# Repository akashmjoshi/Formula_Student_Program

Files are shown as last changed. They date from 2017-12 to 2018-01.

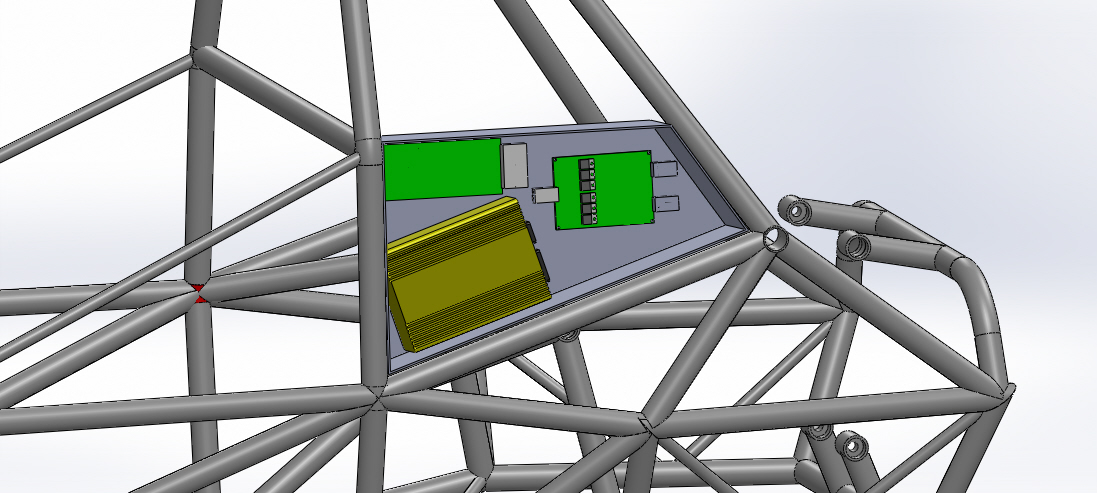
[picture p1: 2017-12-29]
documents/images/electronic assembly.JPG

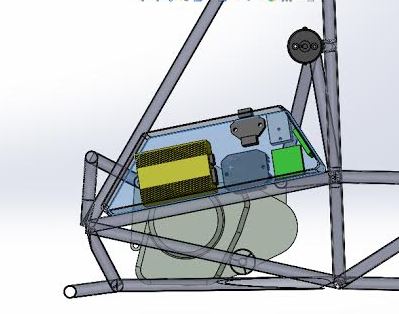
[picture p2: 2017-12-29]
documents/images/ELectronic_hub_casing_CAD.JPG

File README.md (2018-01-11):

# Formula_Student_Program
# Responsiblity
• Established CAN communication with Motec M400 (ECU) to display real-time sensor data on the steering-wheel
• Designed and manufactured a non-contact infrared tire-temperature and brake disc temperature data logger
• Performed Gear-Change Ignition Cut using a electronic-solenoid to perform clutch-less gear shifting
• Tuned the fuel and ignition maps during chassis-dyno to achieve a flat torque curve and optimize fuel efficiency  
•  Created a Wiki-System to allow proper flow of data among all subsystems of the team - https://sites.google.com/a/orion-racing.com/orion-wiki-test/

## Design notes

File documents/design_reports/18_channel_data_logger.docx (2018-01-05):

Data Acquisition System

Power Supply : A 12 V Li ion (or li po. Not sure) rechargeable battery is used. The battery can power t Data acquisition system for up to 7 hours continuously with full charge. The battery was incorporated to keep the DAQ an independent unit on the car.

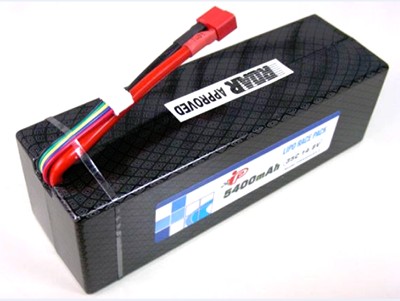
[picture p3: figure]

Power Card: The output of the power card is 3.3 V and 5 V. The voltages were chosen because

1) The dspic controller works on 3.3V
2) The ICs work on 5V supply

All the sensors are given 3.3V as supply voltage.

Parallel Port connectors are used to make the wiring and connections neater and less troublesome.

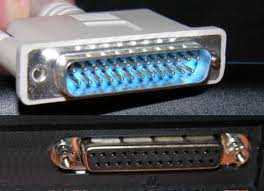
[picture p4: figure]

The Main Control board:

DAQ uses Dspic microcontroller. Some specification of the controller is shown below

Dspic33fj128gp706a

Device Pins: 64

Program : 128Kb

Flash:

Memory

(Kbyte)

RAM

(Kbyte)(1)

16-bit Timer

Input Capture

Output Compare

Std. PWM

Codec

Interface

ADC

UART

SPI

I2C™

Enhanced

CAN

I/O Pins (Max)(2)

Packages

The data collected from the sensors is analog in nature. The data is then converted into digital data using the ADC. The resolution of the system is 0.8mV.The data is then calibrated using equations which are acquired using Matlab. The data is then stored in Flash drive and is also seen on hyper terminal wirelessly.

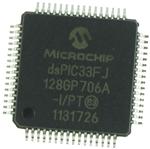
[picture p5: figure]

Modes of Logging Data:

1) USB Flash Drive using VINCULUM V Drive 2

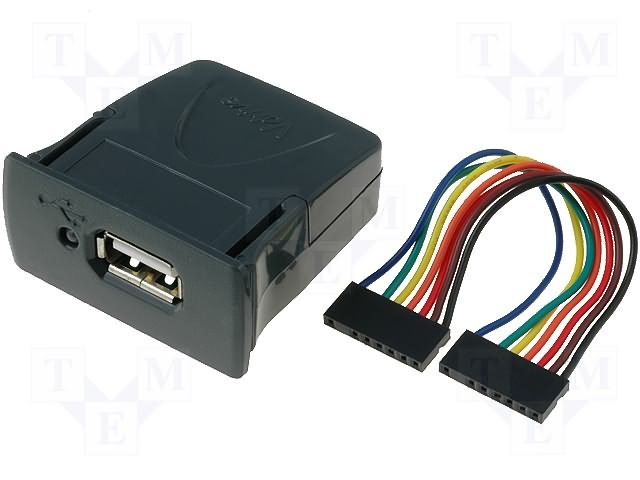
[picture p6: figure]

The Data from the Adc is stored in the Vdrive using Uart protocol. The baud rate for data transmission was set at 230400 for 4 channels. For the channels to be increased from 4 to 18 the baud rate was sacrificed and brought down to 38400.

The data acquired is stored in the USB flash drive in the form of an excel sheet in .xls format which can be easily viewed and analyzed.

2)Telemetry using X bee.

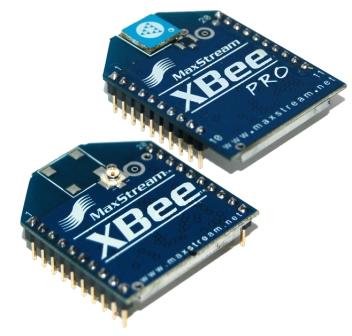
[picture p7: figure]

The data is seen live on the hyper terminal using xbee and the baud rate of the xbee was kept at 57600 even after changing the number of channels.

Indoor/Urban Range Up to 100 ft (30 m) Up to 300 ft. (90 m), up to 200 ft (60 m) International

variant

Outdoor RF line-of-sight Range Up to 300 ft (90 m) Up to 1 mile (1600 m), up to 2500 ft (750 m)

international variant

Transmit Power Output

(software selectable) 1mW (0 dBm) 63mW (18dBm)*

10mW (10 dBm) for International variant.

The data is also seen on the GUIs which are made on Labview. They are used for the ease of Analyzing.

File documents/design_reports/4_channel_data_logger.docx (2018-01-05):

DESIGN REPORT

ELECTRONICS

DATA ACQUISITION SYSTEM

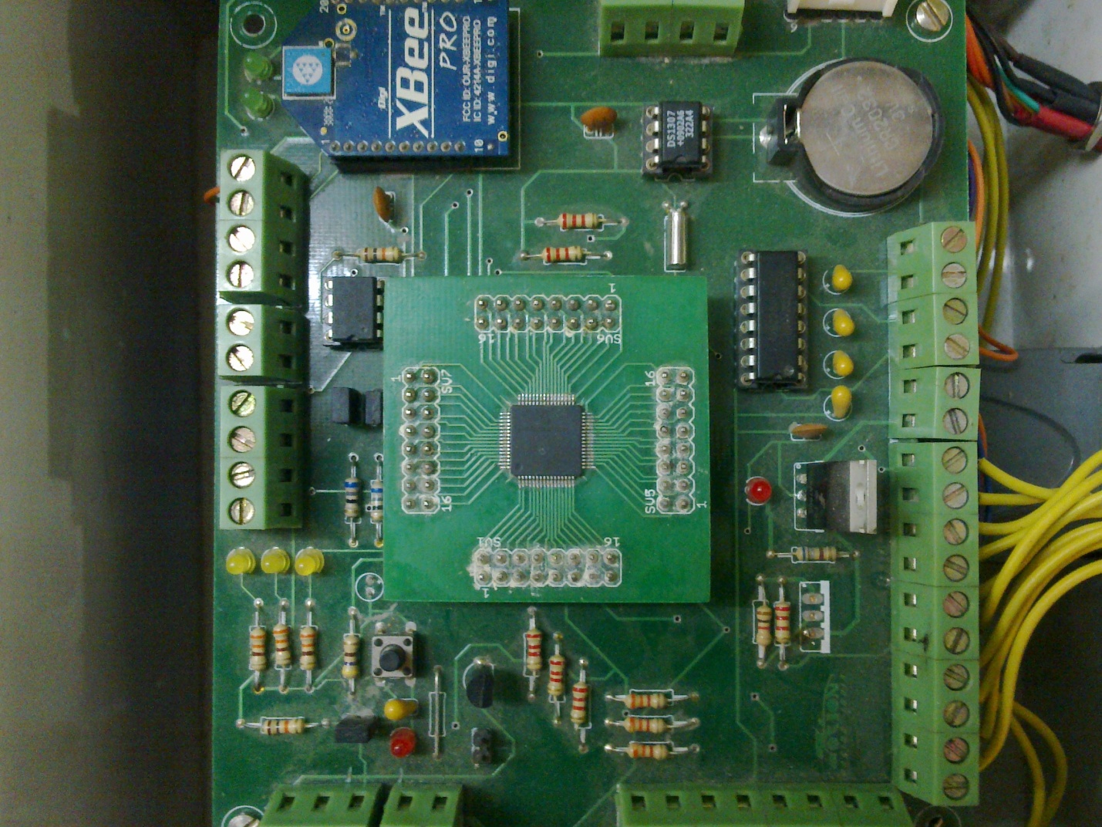
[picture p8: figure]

At present our data acquisition system uses a DSPIC33FJ128GP706A microcontroller. It has 18 analog channels which take in analog voltages and converts it into digital data and stores it into a USB flash drive

Last year the capacity of our data acquisition system was four channels. This year we modified the code and now the capacity has increased to eighteen channels, allowing us top log eighteen different sensors simultaneously.

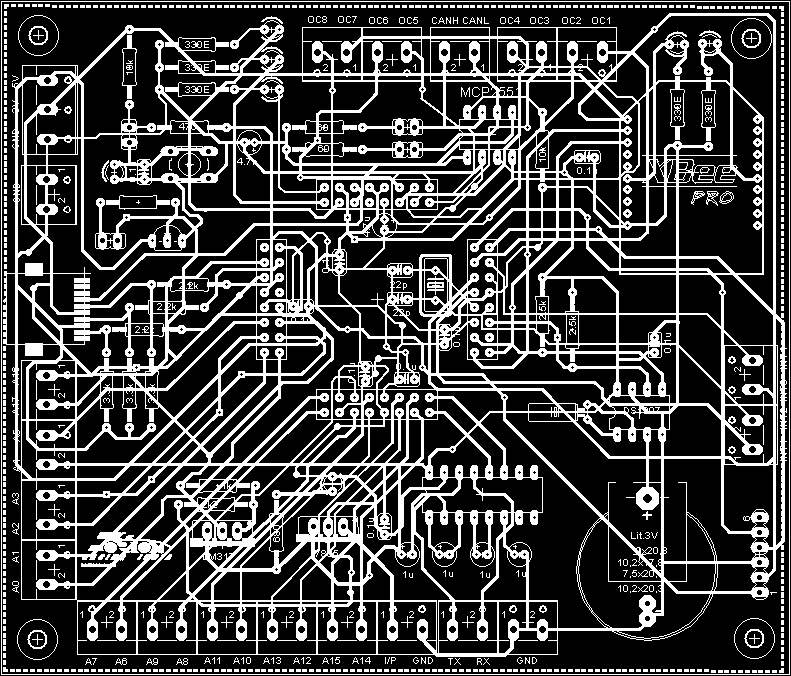
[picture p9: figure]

Since last year the DAQ had only four channels, the logging rate for the system was 125Hz, which was quite high. But now we have increased the number of channels to 18 thus the logging rate had to be reduced. In order to perfectly log the data we have kept the logging rate to 25Hz. Due to this change our baud rate had to be modified to 38400 from 57600. We are using a peripheral device called VDRIVE to log the data into the flash drive from the microcontroller. VDRIVE acts as the interface between the microcontroller and the flash drive. VDRIVE supports the USB 2.0 protocol.

The casing of our DAQ is too large and has unnecessary space. So this year we decided to change the casing of the DAQ. We have reduced the size of the casing and also changed the colour of the box to black so it would go better with the surroundings. The new case of the DAQ has helped us to save space and also to reduce weight.

Acquisition

1. STS

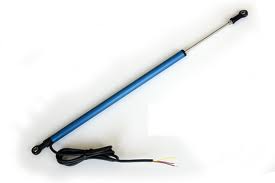
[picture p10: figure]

Shock travel sensor is a linear potentiometer which provides voltage as output

proportional to the position of the slider. When the wheel lifts up from the ground shaft of the sensor tends to move which in turn provides output in terms of voltage. This voltage is sent to the analog channel pin of the micro controller. Use: Suspension

2. ACCELEROMETER

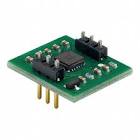
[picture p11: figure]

Accelerometers are used for measuring the g-force experienced by a body. The accelerometer that we use has the capability to measure all the 3-axis viz x,y,z.

The maximum g-force that can be measured by our accelerometer is 3g which is sufficient for our purpose. This voltage is sent to the analog channel pin of the micro controller.

Use: Chassis System

3. Steering Angle Sensor

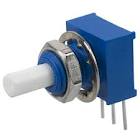
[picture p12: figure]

This is a rotational potentiometer. The output is an analog varying voltage which changes according to the angle of the steering wheel. This voltage is sent to the analog channel pin of the micro controller.

Use: Steering System

4. Gear Position Sensor

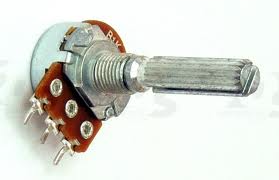
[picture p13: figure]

This is a rotational potentiometer. The output is an analog varying voltage which changes according to the angle of the steering wheel. This voltage is sent to the analog channel pin of the micro controller.

Use: Engine System

5. Fuel Level Indicator

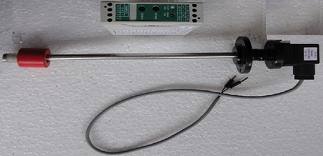
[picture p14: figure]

This is an angular potentiometer. There is a shaft that varies with the level of the fuel. Corresponding to that a analog voltage is produced. This voltage is sent to the analog channel pin of the micro controller.

Use: fuel tank

6. Wheel Speed Sensor

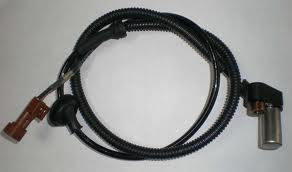
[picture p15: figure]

The wheel speed sensor provides us with the information to calculate the wheel speed of the automobile. Our wheel speed sensor works on the Hall effect principle. It provides us with PWM pulses. These pulses can be directly sent to the PWM pins of the microcontroller which can then be logged in the usb flash drive. We can also use a RC network to convert the PWM pulses to analog voltage and then log it in our system.

Use: Suspension

7. Break Pressure Sensor

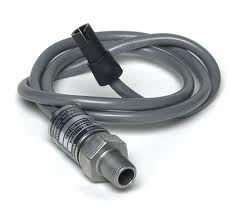
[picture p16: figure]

The brake pressure sensor provides the information about the pressure applied on the brake pedal. The output of this sensor is a varying current. We will be using an I to V converter in order to log data from this sensor. This voltage is sent to the analog channel pin of the micro controller.

Use: Brake System

Calibration of the sensors was done to ensure proper output. We used MATLAB and LABVIEW to calibrate the sensors. Our microcontroller has a 12-bit ADC. Thus we get a digital output of 0-4095 corresponding to analog voltage of 0-3.3 respectively. We took various reading of the sensor using live telemetry and with the help of LABVIEW. We noted down the readings of the sensor output and plotted the graph in MATLAB. MATLAB was able to provide us with the equation of the graph. Now in our daq code we inserted that equation and hence we were able to take proper reading of the sensor

WIRING

Previously for the relays and the fuses we had separate boxes. This arrangement made troubleshooting difficult for us. To overcome this problem what we have done is that we mounted all the relays on the firewall. This has made assembling the relays and the wiring easier. Also now we have a separate fuse case for every fuse as opposed to last year’s fuse box. This way routing the wires has become easier and also it has helped us to reduce the length of the wires.

Another improvement that we have made is the use of heat shrinks. Last year we had used wire sleeves. The problem with wire sleeves was that due to bending of the wires there was a chance that the wires would snap. The heat shrinks do not pose any problem as such. Another advantage of heat shrinks is that they look good aesthetically, they go with the car.

Majority of the wiring has been done using 4mm gauge wire. The starter motor, main kill and fuel pump have been wired using 8mm wire gauge.

The dashboard contains switches for the MOTEC(our ECU), kill, fan, cooling pump, rain-mode and the lcd.

We bought these professional type connectors. But then we realised later that these are not suitable for our task as the crimps were getting loose all the time and we were facing connectivity issues. The crimps would incessantly become loose and would come out of its connector. The new connectors that we bought solved that problem, they are better because the crimps do not get loose and connectivity is maintained during running of the car.

The wiring has also increased as the DAQ has eighteen channels and so all the 18 analog channel needs to be wired with its respective sensor.

DRIVER INTERFACE

LCD on the steering wheel: we are mounting a 20*4 LCD on the steering wheel to display information to the driver. The information to be displayed includes speed, distance, fuel level, gear position. The LCD is controlled by a PIC18F4520 microcontroller. This controller was chosen because of its ability to get data from 13 different channels using one inbuilt analog to digital convertor. The LCD is controlled in a 4 bit mode for port optimization. Data is taken from the engine as well as the sensors attached on the car. This data is then calibrated and displayed on the LCD. Odometer is also being displayed on the LCD screen and to achieve that we have used the FLASH Memory of the controller to store the odometer reading so that the data is not lost after power off. The LCD code is designed in such a way that a small switch is used to switch the screen from one to another on the same LCD.

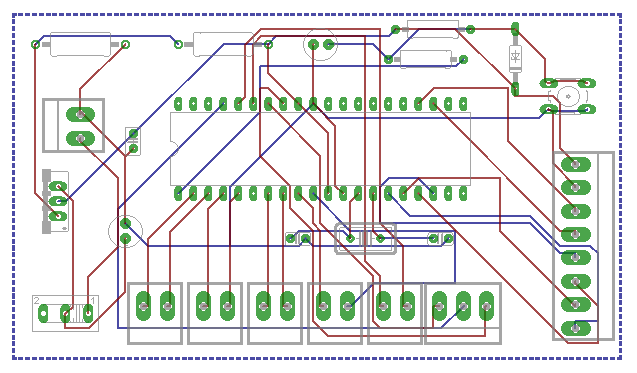
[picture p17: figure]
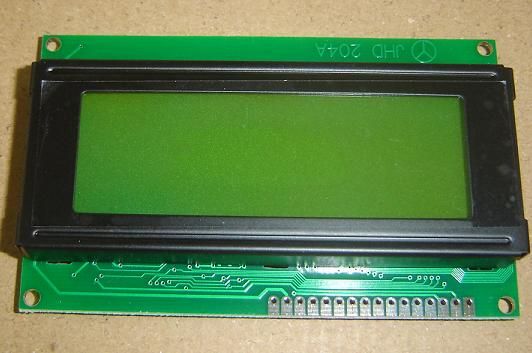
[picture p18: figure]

RPM SHIFT LIGHTS: This year instead of having two separate circuits for the LED’s we are using a single circuit. This way it saves power and space. The steering wheel does not have enough spacing for a pcb as large as last year’s so we have made a small circuit. We need last year’s circuit photograph for comparison

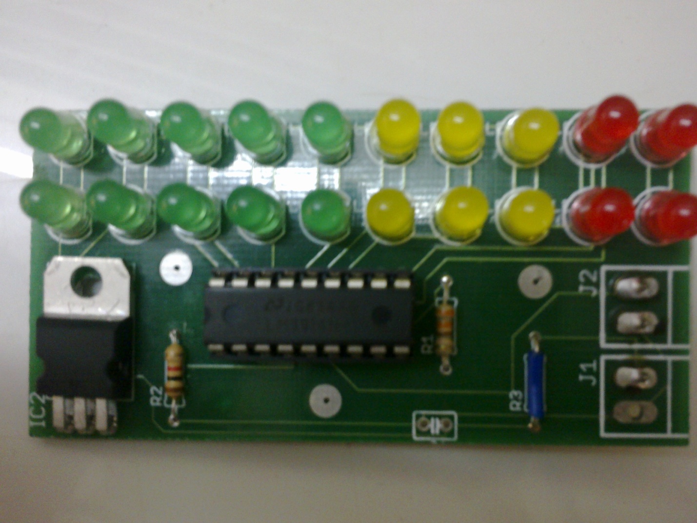
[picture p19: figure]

The circuit consists of LM 3914 which is a bar/dot display driver. A maximum of 10 led’s can be driven. The LED’s are driven according to the voltage variation at the signal pin of the IC which is pin no.5. The signal from the ECU for engine revolution was a varying frequency signal. We thought of using a capacitor with a bleeder resistor but it did not work out. We are now using IC LM 2907 which is a frequency to voltage convertor. This IC converts the frequency from the signal and converts it into analog voltage at 1V/67Hz. LM 7808 is used for regulated voltage supply to the IC.

RPM Shift Lights lets the driver know when to shift gear through the lighting of the led’s giving him a rough idea of the engine rpm.

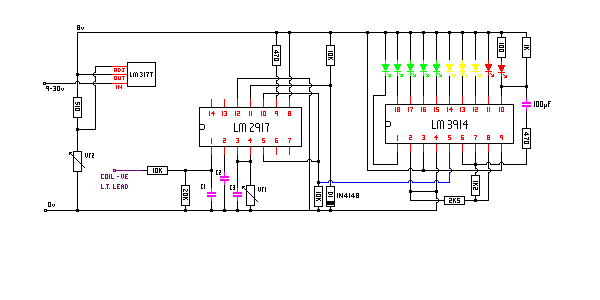
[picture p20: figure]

FUTURE IMPROVEMENTS:

We have decided to use a graphic LCD display for next year for better visual display for the driver while driving the car. Implementation of RPM shifts lights on the LCD controller itself. This can be achieved by reducing the number or channels and making a PORT on the controller available for RPM output.

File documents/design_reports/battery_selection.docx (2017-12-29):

CHAPTER 2: BATTERY

System Needs

ECU MoTec M400

- The power is distributed among the fuel pump, ignition coils and injectors, and ignition module.
- The fuel pump consumes 8 amps @ 12 Volts to maintain fuel pressure at 50 psi.
- The injectors’ ohm values lie between 11.9 to 12.1 ohms. Considering 12.1 ohms resistance and battery voltage of 13.7 volts at idle, the average current consumed will be 1.13 amps.
- The ignition coils consumes 6 amps of current at every spark cycles.
- Total 15.13 amps of current is required.

Cooling System

- The cooling system consists of 2 motors; one used for the radiator fan and the second used as a water pump.
- The water pump motor is run at 5.7amps.
- The radiator fan motor consumes 5.5 amps
- Total 11 .2 amps of current is required.

The current required for gear position system and SLM consumes maximum 3 amps of current.

The cranking current is typical 35 amps of current, but this much current is needed only at the time of cranking. Therefore of 35 amps of current is required for 2 to 3 seconds.

Total maximum of 29.33 amps of current is needed for all systems to work properly.

During the testing sessions once the alternator was failed. Testing logs are as shown in fig.1

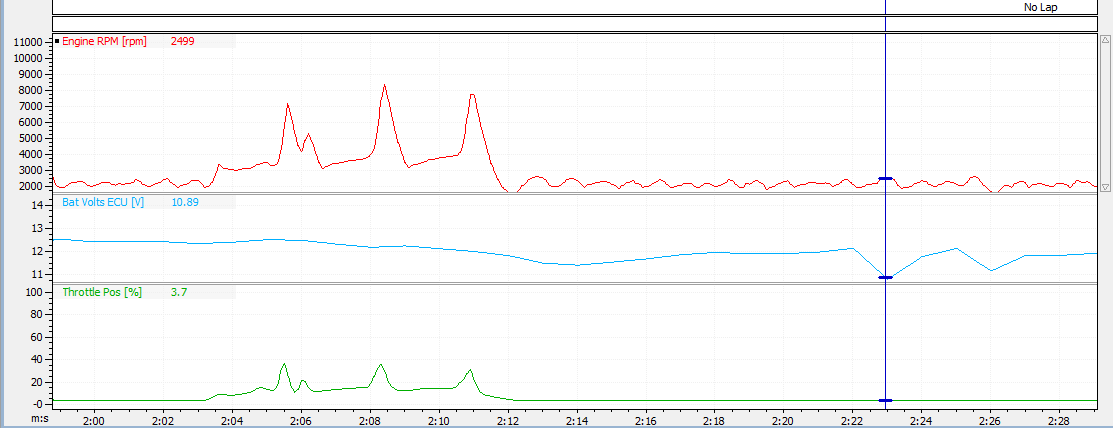
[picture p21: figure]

Fig.2.1

In case of accidental improper function of alternator, battery is supposed to provide 29.33 amps of current. Considering 96 seconds for one lap, 18 laps will takes 1728 seconds that is 28.8 minutes to complete the event. So battery is supposed to give at least 29.33 amps of current. Therefore we decided to use a 21 Ah battery which will be able to supply 42 ampere of current which will ensure the event gets completed with alternator failure.

The battery is placed between primary and secondary fire wall, and we have provision to remove the secondary fire wall as shown in the fig.2. Hence the battery can be easily accessed from outside after the removal of driver seat.

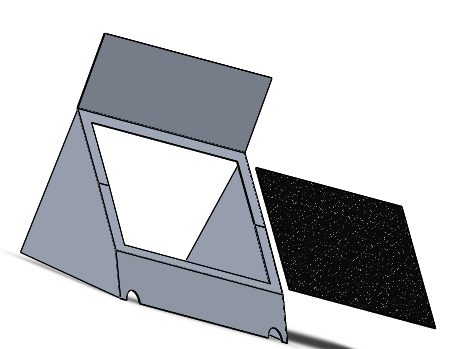
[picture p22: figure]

Fig.2.2

By giving the easy access to the battery, the debugging is also easy. So the debugging time gets reduced.

THE DECISION OF SELECTING LITHIUM ION BATTERY

The battery used in most cars is lead acid batteries but these prove to be too heavy for a formula student race car. Batteries need to be lighter and compact for better weight reduction and still provide the needed performance. The batteries need to be rechargeable through a rectifier connected to the alternator of the engine. Hence to justify our battery selection various decision and analysis were made.

Battery Selection Criteria

- Battery Weight : Lesser the better
- Battery Capacity (AH) : More the better
- Battery Discharge rate (Amp) : Less the Better
- Battery Cost : Less the better
- Battery Size (Volume) : Less the better

The Ah number indicates how many amps (how much current) a battery can supply over a given period of time. It's sort of the gas gauge of a battery's fuel tank. The higher the number, the more likely the battery will deliver prolonged performance.

We made a decision matrix as shown below to give weightages to the parameters which were more important than the other.

| weight | Discharge | cost | size
Weight | 1 | 1 | 1 | 0
discharge | 1 | 1 | 0 | 0
Cost | 1 | 0 | 1 | 0
Size | 0 | 0 | 0 | 1
Total | 3 | 2 | 2 | 1
weightage | 37.5 | 25 | 25 | 12.5
| | Table.2.1
Chemistry | weight | Discharge | cost | size
Lead Acid | 0 | 0 | 1 | 0
Lithium-iron | 1 | 1 | 0 | 1
Weighted | Weight | Discharge | Cost | Size | Total Score
Lead acid | 0 | 0 | 25 | 0 | 25
Lithium-iron | 37.5 | 25 | 0 | 12.5 | 75

Table.2.2

Here in table.1 we gave weightages to the parameters. The weightage points have been normalizes to a total of 100 points.

In table.2 we have compared Lead Acid Battery with the Lithium-ion battery. These batteries were found suitable by us for automotive use.

Adding up the scores from table one and two, we can see that the weightage total of the scores for Lithium-iron is higher than lead acid battery by 50 points. Advanced chemistry batteries include LiFePO4 batteries and Li Ion batteries. Batteries of these chemistries were found suitable by us for automotive use. Adding up the scores from table one and two, we can see that the weightage total of the scores for advanced chemistry is higher than lead acid battery by 50 points. Thus we justified the use of Advanced Chemistry batteries.

Shorai and braille were the two reliable batteries which we found suitable for automotive use. A comparison of shorai with the braille battery is as shown below. We have represented advanced chemistry batteries with the braille battery.

battery chemistries | Weight | discharge | | cost | size
LiFePO4 (Shorai) | 1 | 0 | | 1 | 1
Li Ion (Braille) | 0 | 1 | | 0 | 0
TOTAL | 1 | 1 | | 1 | 1
WEIGHTAGE | 25 | 25 | | 25 | 25
| | Table2.3
Weighted | Weight | Discharge | Cost | | Size | Weighted Score
LiFePO4 (Shorai) | 25 | 0 | 25 | | 25 | 75
Li Ion (Braille) | 0 | 25 | 0 | | 0 | 25

Table.2.4

Thus we have selected SHORAI LFX21A6-BS12. This battery weighs 1410 grams which is 740 grams higher than previous year’s battery. This was the compromise made in the battery selection procedure.

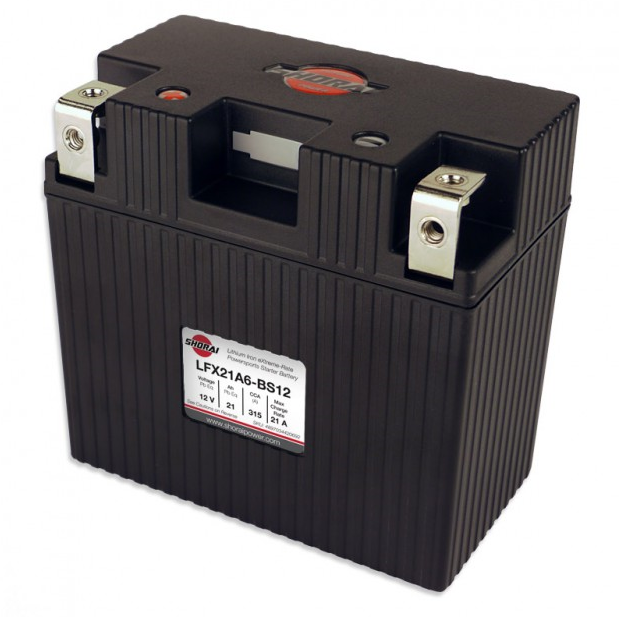
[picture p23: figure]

Advantages of using the selected battery:

- Ultra-light. One Fifth the weight of convectional batteries on average (1.41 kg/7.11kg)
- Zero sulfation, for longer service life
- More current for burst: (315 Amps)
- Military spec Carbon Composite Case
- Fast charging for better cranking
- No explosive gasses during charge
- No need of using a BMS

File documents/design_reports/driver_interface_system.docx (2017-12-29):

CHAPTER 4: DRIVER INTERFACE SYSTEM

Design Targets

1. Vehicular Interaction with the driver

Showing vital information to the driver such as rpm, engine temp, oil pressure, speed and fuel used.

2. Ergonomically placed steering system and dashboard

The way a driver interacts physically with the car is also important. This means the location of the steering wheel, the dashboard and shifter link play major role in driving feasibility. Thus an ergonomically designed driver interface system is a must.

3. Compactness and vehicular integration

The use of CAD models during PCB design to formulate a well-designed and compact system

System Design

The electronics system was designed along with the 3d model of the car which proved to be very reliable. The electronics systems are placed within the secondary and the primary firewall. This assured the temperatures never reached more than 60 degrees. The compactness of the secondary firewall provided a safety factor for the systems.

Secondly a high speed microcontroller was used to achieve refresh rates 67Hz as compared to 1Hz in our previous design. Sensor calibration was achieved using 5 point calibration technique to prevent linear hysteresis.

Electronics hardware integration within the steering wheel made the design and handling very user-friendly. The dashboard was made ergonomically and acquire minimum space and the cause least driver interference.

CAD / 3d part files and assembly was done on Solidworks to achieve accurate integration with other systems and it also provided an overlay for the wiring harness. The use of CAD was done for the first time and it proved really helpful in design and manufacturing.

Dashboard

The dashboard consist 3 switches; the cockpit kill switch, the cooling switch and the ignition switch. These are ground activated switches and are used to turn on relays. The cockpit kill switch is a push to break switch and disconnects the power supply to the ECU M400. This in turn turns off the supply to the fuel and ignition system thus stopping the engine.

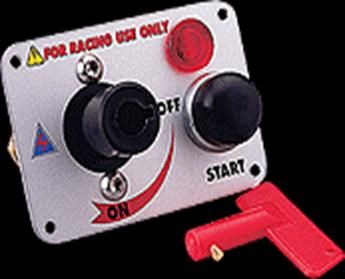
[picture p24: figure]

Fig 4.1

External Kill Switch

The cooling switch turns on and off a PCB mountable relay which in turn switch on or off the cooling centrifugal pump or the cooling fan.

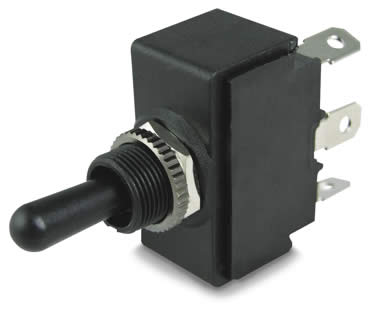
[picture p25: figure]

Fig 4.2

Cooling Switch

The ignition switch is ground connected to the automotive starter motor relay. The switch is a momentary switch and pressing the switch turns on the stator motor which help the engine to crank and synch the crankshaft and the flywheel.

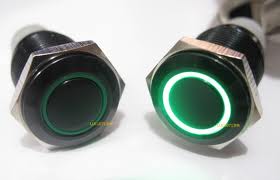
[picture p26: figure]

Fig 4.3

Ignition Switch

Steering Display System

The design phase started with what parameter was to be displayed on the screen.

The steering wheel is one of the most important parts of a formula race car. It needs to show vital engine parameters to the drivers during a long endurance run. The steering wheel is made of 7 series aluminum and the electronic system consists of a 7 segment display for showing gear. Two 4 digit 7 segment displays to show different engine parameters of the engine. There is a 16 bit RPM/GSL LEDs to tell the driver when to shift to get maximum torque in the next gear.

| | | | | | | | Output Shaft Torque
RPM | | Engine torque | | | | 1st | 2nd | 3rd | 4th | 5th | 6th
| | | | HP | Ratio :1 -> | 2.833 | 2.062 | 1.647 | 1.421 | 1.272
2000 | | 13.27 | | 5.1 | | 38 | 27 | 22 | 19 | 17 | 0
3000 | | 19.914 | | 11.4 | | 56 | 41 | 33 | 28 | 25 | 0
4000 | | 25.814 | | 19.7 | | 73 | 53 | 43 | 37 | 33 | 0
5000 | | 33.19 | | 31.6 | | 94 | 68 | 55 | 47 | 42 | 0
6000 | | 37.614 | | 43.0 | | 107 | 78 | 62 | 53 | 48 | 0
7000 | | 42.778 | | 57.0 | | 121 | 88 | 70 | 61 | 54 | 0
8000 | | 44.327 | | 67.5 | | 126 | 91 | 73 | 63 | 56 | 0
9000 | | 42.778 | | 73.3 | | 121 | 88 | 70 | 61 | 54 | 0
10000 | | 37.615 | | 71.6 | | 107 | 78 | 62 | 53 | 48 | 0
12000 | | 31.715 | | 72.5 | | 90 | 65 | 52 | 45 | 40 | 0

NOTE : The chart at left will help you find what RPM's each gear will jump to. It takes the gear ratios you entered, then calculates what RPM the next gear gives you. In the default scenario, if you shift at 5600 in each gear, then going to 2nd will drop you to 3300, from 2 to 3 (at 5600rpm) gets you at 3771, and so on.

To navigate, using the TAB key will produce the best results, and data entry areas are in blue.

This worksheet is protected, but no password is required . The BASELINE and DISCLAIMER are password protected.

Shift RPM

RPM after shift
| | | | | | | 1 - 2 | 2 - 3 | 3 - 4 | 4 - 5 | 5 - 6
| | | | | | 2000 | 1456 | 1597 | 1726 | 1790 | 0
| | | | | | 3000 | 2184 | 2396 | 2588 | 2685 | 0
| | | | | | 4000 | 2911 | 3195 | 3451 | 3581 | 0
| | | | | | 5000 | 3639 | 3994 | 4314 | 4476 | 0
| | | | | | 6000 | 4367 | 4792 | 5177 | 5371 | 0
| | | | | | 7000 | 5095 | 5591 | 6039 | 6266 | 0
| | | | | | 8000 | 5823 | 6390 | 6902 | 7161 | 0
| | | | | | 9000 | 6551 | 7189 | 7765 | 8056 | 0
| | | | | | 10000 | 7279 | 7987 | 8628 | 8951 | 0
| | | | | | 12000 | 8734 | 9585 | 10353 | 10742 | 0

Fig 4.4

RPM v/s Horse Power

The microcontroller used to control the display unit is a PIC18F6720 microcontroller. The microcontroller has timer circuits to detect RPM and analog channels to measure engine sensor values. This microcontroller was chosen based on its ability to provide a range of input output ports.

Microcontroller Specifications

High-Performance RISC CPU:

• C compiler optimized architecture/instruction set:

- Source code compatible with the PIC16 and PIC17 instruction sets

• Linear program memory addressing to 128 Kbytes

• Linear data memory addressing to 3840 bytes

• 1 Kbyte of data EEPROM

• Up to 10 MIPs operation:

- DC – 40 MHz osc./clock input

- 4 MHz – 10 MHz osc./clock input with PLL active

• 16-bit wide instructions, 8-bit wide data path

• Priority levels for interrupts

• 31-level, software accessible hardware stack

• 8 x 8 Single Cycle Hardware Multiplier External Memory Interface (PIC18F8X20 Devices Only):

• Address capability of up to 2 Mbytes

• 16-bit interface

Peripheral Features:

• High current sink/source 25 mA/25 mA

• Four external interrupt pins

• Timer0 module: 8-bit/16-bit timer/counter

• Timer1 module: 16-bit timer/counter

• Timer2 module: 8-bit timer/counter

• Timer3 module: 16-bit timer/counter

• Timer4 module: 8-bit timer/counter

• Secondary oscillator clock option – Timer1/Timer3

• Five Capture/Compare/PWM (CCP) modules:

- Capture is 16-bit, max. Resolution 6.25 ns (TCY/16)

- Compare is 16-bit, max. Resolution 100 ns (TCY

- PWM output: PWM resolution is 1 to 10-bit

• Master Synchronous Serial Port (MSSP) module with two modes of operation:

- 3-wire SPI™ (supports all 4 SPI modes) 2-I C™ Master and Slave mode

• Two Addressable USART modules:

- Supports RS-485 and RS-232

• Parallel Slave Port (PSP) module

Analog Features:

• 10-bit, up to 16-channel Analog-to-Digital Converter (A/D):

- Conversion available during Sleep

• Programmable 16-level Low-Voltage Detection (LVD) module:

- Supports interrupt on Low-Voltage Detection

• Programmable Brown-out Reset (PBOR)

• Dual analog comparators:

- Programmable input/output configuration

Special Microcontroller Features:

• 100,000 erase/write cycle Enhanced Flash program memory typical

• 1,000,000 erase/write cycle Data EEPROM memory typical

• 1 second programming time

• Flash/Data EEPROM Retention: > 40 years

• Self-reprogrammable under software control

• Power-on Reset (POR), Power-up Timer (PWRT) and Oscillator Start-up Timer (OST)

• Watchdog Timer (WDT) with its own On-Chip RC Oscillator for reliable operation

• Programmable code protection

• Power saving Sleep mode

• Selectable oscillator options including:

- 4X Phase Lock Loop (of primary oscillator)

- Secondary Oscillator (32 kHz) clock input

• In-Circuit Serial Programming™ (ICSP™) via two pins

• MPLAB ® In-Circuit Debug (ICD) via two pins


Fig 4.6

Driver Interface system


Fig 4.7

Steering Wheel

Coding and Testing

The code was written using Mikroc along with simulation in Proteus

Code:

//Decleration and Initialization

#include <built_in.h>

char ur,tr,hr,thr,ul,tl,hl,thl; //segment choping variables

int count,i,j,value,rpm,gearp;

char teeth;

int volt,etmp,as,ts;

int seg7(int num)

{

int val[]={0x3f,0x06,0x5b,0x4f,0x66,0x6D,0x7D,0x07,0x7F,0x6F,0x77,0x7C,0x39,0x5E,0x79,0x71};

return(val[num]);

}

int gear(int num)

{

int val[]={0x54,0x06,0xDA,0xCE,0x66,0xEC,0xFC,0x86,0xFE,0xEE};

return(val[num]);

}

int fun(int num)

{

int val[]={0x7f,0x3f,0x1f,0x1e,0x1c,0x18,0x10,0x18,0x1c,0x1e,0x1f,0x3f,0x7f,0x00,0x7f};

return(val[num]);

}

int bar(int num)

{

int val[]={0x81,0xc3,0xe7,0xff,0xe7,0xc3,0x81,0x81,0xc3,0xe7,0xff,0xe7,0xc3,0x81};

return(val[num]);

}

int gps()

{

j=ADC_READ(3);

if (j>=0 &&j<88)

{PORTB=gear(1);

return 1;}

// else if (j>=151 && j<159)

// {PORTB=gear(0);

// return 0;}

else if (j>=89 && j<284)

{PORTB=gear(2);

return 2;}

else if (j>=285 && j<499)

{PORTB=gear(3);

return 3;}

else if (j>=500 && j<700)

{PORTB=gear(4);

return 4;}

else if (j>=700 && j<897)

{PORTB=gear(5);

return 5;}

else if (j>=898 && j<1020)

{PORTB=gear(6);

return 6;}

}

int et()

{

j= ADC_Read(0); //engine temp begins

return etmp= (6.4*j*j/100000 +-0.19*j + 126);

}

speed()

{

value=TMR1H;

//use timer 1 for speed anf fuel used calculations

}

fuelused()

{

//use timer 1 for speed anf fuel used calculations

}

rpmlights(int num)

{

switch(num)

{

case 1: PORTF=0x01; break;

case 2: PORTF=0x01; break;

case 3: PORTF=0x01; break;

case 4: PORTF=0x03; break;

case 5: PORTF=0x07; break;

case 6: PORTF=0x1f; break;

case 7: PORTF=0x3f; break;

case 8: PORTF=0x7F; break;

case 9: PORTF=0xff; break;

case 10: PORTF=0x1c; break;

case 11: PORTF=0x1C; break;

case 12: PORTF=0x1C; break;

}

}

segr()

{

thr=value/1000;

hr=value/100%10;

tr=value/10%10;

ur=value%10;

if(value>999)

{

RC7_bit=1;

RC6_bit=0;

RC5_bit=1;

RC4_bit=1;

PORTD=seg7(thr);

delay_us(1000);

}

if(value>99)

{

RC7_bit=0;

RC6_bit=1;

RC5_bit=1;

RC4_bit=1;

PORTD=seg7(hr);

delay_us(1000);

}

if(value>9)

{

RC7_bit=1;

RC6_bit=1;

RC5_bit=1;

RC4_bit=0;

PORTD=seg7(tr);

delay_us(1000);

}

if(value>=0)

{

RC7_bit=1;

RC6_bit=1;

RC5_bit=0;

RC4_bit=1;

PORTD=seg7(ur);

//delay_us(2500);

}

}

segl()

{

thl=value/1000;

hl=(value/100)%10;

tl=value/10%10;

ul=value%10;

if(value>999)

{

RG3_bit=1;

RG2_bit=0;

RG1_bit=1;

RG0_bit=1;

PORTE=seg7(thl);

delay_us(1000);

}

if(value>99)

{

RG3_bit=1;

RG2_bit=1;

RG1_bit=1;

RG0_bit=0;

PORTE=seg7(hl);

delay_us(1000);

}

if(value>9)

{

RG3_bit=1;

RG2_bit=1;

RG1_bit=0;

RG0_bit=1;

PORTE=seg7(tl);

delay_us(1000);

}

if(value>=0)

{

RG3_bit=0;

RG2_bit=1;

RG1_bit=1;

RG0_bit=1;

PORTE=seg7(ul);

//delay_us(2500);

}

}

void coolon()

{

RG3_bit=1;

RG2_bit=0;

RG1_bit=1;

RG0_bit=1;

PORTE=0x39;

delay_us(4000);

RG3_bit=1;

RG2_bit=1;

RG1_bit=0;

RG0_bit=1;

PORTE=0x3F;

delay_us(4000);

RG3_bit=0;

RG2_bit=1;

RG1_bit=1;

RG0_bit=1;

PORTE=0x54;

delay_us(4000);

}

void cooloff()

{

RG3_bit=1;

RG2_bit=0;

RG1_bit=1;

RG0_bit=1;

PORTE=0x39;

delay_us(4000);

RG3_bit=1;

RG2_bit=1;

RG1_bit=0;

RG0_bit=1;

PORTE=0x3F;

delay_us(4000);

RG3_bit=0;

RG2_bit=1;

RG1_bit=1;

RG0_bit=1;

PORTE=0x71;

delay_us(4000);

}

void engoff()

{

RC7_bit=1;

RC6_bit=0;

RC5_bit=1;

RC4_bit=1;

PORTD=0x79;

delay_us(4000);

RC7_bit=1;

RC6_bit=1;

RC5_bit=1;

RC4_bit=0;

PORTD=0x3F;

delay_us(4000);

RC7_bit=1;

RC6_bit=1;

RC5_bit=0;

RC4_bit=1;

PORTD=0x71;

delay_us(4000);

}

void main() {

T0CON=0XF8; // timer0 on, 8 bit mode, counter, falling edge, with no prescalar

T1CON=0x0B;

TRISA=0xFF;

ADCON1=0x00;

TRISF = 0;

TRISE = 0;

TRISB = 0;

TRISD = 0;

TRISC0_BIT=1;

TRISC1_BIT=1;

TRISC2_BIT=1;

TRISC3_BIT=1; // 1's inputs

TRISC4_BIT=0;

TRISC5_BIT=0;

TRISC6_BIT=0;

TRISC7_BIT=0; // 0's outputs

TRISG = 0x00;

for(i=0; i<=14; i++)

{

PORTF=bar(i);

PORTB=fun(i);

PORTD=PORTE=fun(i);

PORTG=0X00;

RC4_bit=RC5_bit=RC6_bit=RC7_bit=0;

delay_ms(60);

}

PORTF = 0x00;

while(1)

{

DELAY_MS(16);

gearp=gps();

teeth= TMR0L;

value=teeth*60;

rpm=value/1000;

while(value <1000)

{engoff();

teeth= TMR0L;

value=teeth*60;

if(ADC_Read(1)<= 350)

cooloff();

else

coolon();

}

rpmlights(rpm);

value = et();

segr();

fuelused();

speed();

segl();

// write code for right rotary switch//

TMR0L=0x00;

TMR1H=0x00;

}

}


Fig 4.8

Driver Interface System Simulation

Gear Change Ignition Cut

The MoTeC GCIC function is used to allow the driver to change gears without lifting the throttle or (in most cases) the clutch, it is also often referred to as “Flat Shift” or “Shift without Lift”. The system allows a short ignition or fuel cut and/or ignition timing retard to reduce the engine’s load on the transmission so that the gear can be changed. It is also possible to have the position of an Electronic Throttle (Drive by Wire) reduced for a short amount of time as well.

The function is designed with both H pattern and sequential, dog engagement gear boxes in mind, it should be noted that this function is not completely suitable for synchromesh gearboxes.

Cut Modes

Mode 1, Delay from next gear stable

This mode is only suitable when the ECU has a gear position input. The ignition cut starts as soon as a valid shift signal is detected and will hold for however long it takes for the gear position pot or gear calculation to detect the next gear has been reached or the Minimum RPM or Minimum Throttle Position have been reached. The Delay time starts when the new gear is detected to allow time for full engagement then the ignition is phased back in linearly over the recovery time.


Fig 4.9

Mode 2, Delay from Cut Signal

The Delay from Cut Signal mode starts the ignition cut when the cut source becomes active and runs for the user defined Delay time (as set in Delay Table). After the delay has timed out the ignition Recovery time starts.


Fig 4.10

Mode 3, Cut While Signal is active

This mode will simply cut the ignition for as long as the shift signal is active. No delay times are entered for this mode. Mode 3 is mainly designed for external gear box control systems that are able to send a GCIC signal to the ECU; the cut time is calculated in the external controller.


Fig 4.11

It can be seen from the previous two diagrams that the gear position does not affect the cut at all.

Cut Source

To make the GCIC system work the ECU needs a request that the driver wishes to make an up shift, there are a number of options for this. It is possible that race class rules may only allow certain methods for GCIC so the rule book will need to be checked.

1. A simple momentary (on/off) switch the driver activates when an up shift needs to be made

2. A momentary switch on the clutch pedal

3. The request can be started when the RPM Limiter is reached

4. A strain gauge may be installed on the gear lever

5. The request can be started based on a rate of reduction of throttle position

6. The up shift request can come from the request linked to the Gear Shift function

(“semi-auto” or controlled gearboxes)

How the gear request device or condition is setup can have a very large effect on the performance of the GCIC function. One fairly important aspect of a gearbox that cannot be ignored is the mechanical free play from moving the gear shift lever to moving the dog ring. Another factor is how much force should be used to “preload” the gearbox shift mechanism to get the best shifts. To make a positive shift the driver needs to move to gear lever enough so that all the free play is eliminated and then apply enough force so that when the GCIC starts the gearbox will move almost instantly. Some problems that can arise from incorrect setup of the shift request are:

1. If the request system does not allow the driver to move the gear lever far enough to remove all the free play in the gearbox the GCIC will start too early. Starting the GCIC too early will mean that the total cut time will have to be longer to compensate.

2. If the driver does not have enough “preload” force on the gear lever before the

GCIC starts the gearbox mechanism will not accelerate quickly, again needing a longer cut time to compensate.

3. If too much force is required to start the GCIC the driver may become fatigued or the gear box may be damaged.

1. Digital (Switched) Input

A switched input can be located almost anywhere within reach of the driver but the best logical solution is to have it located on the gear lever. The switch may also be located on the clutch pedal but this may defeat the purpose of GCIC where clutch less shifts are desired. Some racing classes specify a switch location, e.g. steering wheel but this, like a clutch switch, means that the drive must co-ordinate the state of GCIC and the moving of the gear lever correctly and repeatable to get the best performance.

The diagram below shows a basic example of a “double jointed” gear knob for a sequential gearbox where GCIC is only needed on the up shift. The knob is able to pivot for a short distance on the gear lever when pulled towards the rear; this activates the switch giving the ECU its GCIC request. It is recommended that the spring be adjustable for preload so that the correct amount of force can be applied before the GCIC function is started.


Fig 4.12

GCIC Switch

If an H pattern system is needed or GCIC is required for both up and down shifts on a sequential gearbox a dual switch setup can be made.

The switch can be wired to either a Digital input or a Switched (Analogue Temperature) input. A switch wired to a Digital input must connect the input to 0v to pull it low and can be normally open or normally closed, whether the request is active when the switch is open or closed can be selected with the Logic Polarity parameter.

A switch that is wired to a Switched (Analogue Temperature) input can be connected to a voltage higher than 5v as the trigger levels can be defined by the user but it is most common practice to connect the input to 0v via the switch the same as the Digital input. Again a normally open or normally closed switch can be used.

2. RPM Limit

The RPM limiter can be used to request GCIC. The GCIC function request is active when the driver reaches the RPM limit. This method does not require any extra sensors to be added to the car but the driver must be aware that any time they reach the limiter they will get prolonged engine cutting if a gear change is not desired at that time. Delay from next gear stable may not be suitable for this method.

3. Gearshift Force - Strain Gauge

The Strain Gauge works by being bonded onto the surface of an item, its electrical properties change as it is deformed by the small amounts of tension and compression in the item. For GCIC the strain gauge is bonded onto the front or back of the gear lever. As the driver puts force on the gear lever it bends slightly causing a change in signal form the strain gauge.

The voltage signal for a strain gauge is very small and must be amplified to become useful to the ECUs input. When considering bonding a strain gauge onto a gear lever a suitable strain gauge amplifier is needed, this can add a considerable amount to the cost of the system.

The major benefit of the strain gauge is that it is an analogue input with a voltage reading proportional to the drivers force on the gear lever. With the analogue input to the ECU the tuner is able to program the level of force needed to trigger the GCIC request. Another benefit is to be able to data log how the driver is using the gear lever with much more information made available when compared to a simple on/off switch.

The Strain Gauge amplifier’s output can be connected to either an Analogue Voltage input or an Analogue Temperature input although it must be noted that the signal will be slightly non-linear when connected to the Analogue Temperature input due to its internal 1K ohm, 5v pull-up.

When calibrating the Gear Shift Force channel there is no need for the reading to be completely correct as the force level for the request will be set later. As a basic setting the calibration for 5v = 100N will be acceptable, if a more accurate reading is desired a custom calibration (using a fish scale for example) may be required.

4. Throttle Position Reduction

The rate at which the throttle is reduced can be a request for the GCIC function. The request is active when a user defined rate of reduction (TP% per second) of the Throttle Position Channel is reached or exceeded.

This method does not require any additional sensors to be added to the vehicle. Again,

driver education and correct setup is needed as the function will not be able to determine if the driver has lifted the throttle for a gear change or if it is a correction for a loss of traction for example. Again, the delay from next gear stable mode may not be suitable for this method.

Thinking outside the square for experienced users some conditions could be used where no cut is applied (from the cut level table) if there is any wheel slip, allowing the driver to quickly lift the throttle without inadvertently requesting GCIC.

5. Gear Shift Function

The gear box control function will already have a request for an up-shift, so it is possible to link the two functions in software so that the GCIC is automatically triggered when an up-shift request is made by the driver.

6. Minimum RPM

A lower level of RPM is set so that the function cannot be requested. For example, if the car is being driven through the pit lane it would be unnecessary to have GCIC active for the slow shifting needed, the driver would most likely want to use the clutch.

The Minimum RPM can work in different ways in different modes so care must be taken in setup. For the Delay From Cut Signal and Cut While Signal Active modes the Minimum RPM is only a condition that needs to be met at the start of the request and will not affect the cut event once it has been started. For example: If the Minimum RPM is 5000rpm and the engine is at 5050rpm, the GCIC can start. Clearly the RPM will drop as soon as there is any cut. If the engine drops below 5000rpm while the GCIC event is going cut WILL NOT be stopped, the GCIC event will continue for its programmed time.

For the Delay from Next Gear Stable mode the minimum RPM is used in two ways, as a condition to allow the GCIC request to be valid and also as a safety measure for the RPM dropping to low. Because the Delay from Next Gear Stable mode can cut for a much longer time than the other two modes it is possible that the engine may stall if the driver makes a mistake.

7. Minimum Throttle Position

As per Minimum RPM there is also a parameter for a Minimum Throttle Position below which a request is ignored by the ECU. The different mode selected will affect how the Minimum Throttle is use in the same way as the Minimum RPM, for the Delay from Cut Signal and Cut While Signal Active modes the Minimum Throttle is used as a condition to allow the request and start the GCIC event, if the throttle position drops below this value during the GCIC event the cut will not be stopped, for the Delay From Next Gear Stable mode the Minimum Throttle is used as a condition to accept the request and if the throttle drops below this during the GCIC event the cut WILL be stopped.

Delay Table

The Delay Table sets the amount of time the ECU must cut the engine power so that the driver can make a successful shift. The Delay table works in two different ways depending on which Cut Mode is used.

For Mode 1, Delay from Next Gear Stable the request starts the cut and the ECU will continue to cut until the next gear is acquired or the Time Out period has elapsed. The Delay Table sets extra cut duration once the next gear has been reached; this allows time to ensure that the next gear has been successfully engaged. This time is generally short when compared to the Mode 2, Delay from Cut Signal and is often left as 0msecs.

For Mode 2, Delay from Cut Signal the Delay Table sets the time that the ECU cuts the engine power for, this time is started as soon as the cut request becomes active. Enough time must be allowed so that the driver is able to get to the next gear; this mode will not allow for mistakes and will reinstate the engine power after the Delay plus Recovery Time regardless of what position the gear box is in, see example below:


Fig 4.13

Driver Education

For drivers who have spent most of their racing career quickly lifting the throttle to change gear it can be quite difficult to convince them not to lift once GCIC function has been switched on. This can cause problems for the tuner who needs to set minimum and maximum values, especially throttle position, to make the function work. There are many cases of the driver not obeying the instruction to keep the throttle wide open on a shift and this can cause many problems for the logic of the function, below is a common example.

1. The driver has lowered the throttle position until it is well below the Minimum Throttle position.

2. The driver then pulls on the gear lever and is able to change gear with ease because there is no engine torque.

3. Because the driver is still holding enough force on the gear lever as the throttle is reapplied the cut starts. In this example the Mode was Delay from Next Gear Stable meaning that the cut is applied for the full Time Out because the driver triggered the GCIC request after the shift was made and not before.


Fig 4.14

Gear Shift Timing


Fig 4.15

Gear Shift Logged Data

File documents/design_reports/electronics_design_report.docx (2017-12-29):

ELECTRONICS DESIGN REPORT: ORION RACING INDIA

Team goal

While designing the car for reliability, the team looks forward to testing the car extensively for performance. System designs will be validated using sensor data and components will be tested in fatigue. Additionally, the sensors will provide us with data which will help us to tune the car. With the aid of a dynamometer, the aim is to improve and further tune the map table. By physically recreating event specific tracks, the performance of the vehicle is being improved upon.By integrating the above, the team hopes to realize its goal which is to complete and to compete.The design of the car was started by selection of the following three parameters.

1) Tire

Tire has been selected based on the TTC tire data which had 3 tires to compare namely Goodyear D2607, Hoosier and Continental 34M. On comparing the cornering characteristics for the vertical load that was assumed, the Goodyear gave a peak lateral force of 3870 N at 10° slip angle as compared to the Continental which gave a force of 3680 N at 6° slip angle. Keeping in mind the transient response, the Continental tire was selected. On comparing the acceleration characteristics the Continental gave a peak force of 2600N at 5° slip ratio. The low cost and availability of the tires further helped in finalizing the Continental. The increased weight of the Continental tire was a compromise between performance and weight.

2) Engine

With the team goal in mind, the car weight was assumed to be 230 to 240 kg. Thus power to weight ratio was made a main consideration and a 4 cylinder engine with higher displacement became the natural choice. Main criteria while choosing amongst the 4 cylinder engines were availability, torque, familiarity and previous experience. The F4i has 46 Nm of torque (stock) @ 10000 rpm which is more as compared to rest of the engines. The GSX has 46.5 Nm of torque (stock) but at a slightly higher engine rpm i.e. 10750. The peak power of F4i is 109 hp (stock) @ 12500 rpm which is more compared to the other engines. The YR6 has power output of 118 hp (stock) @ 13000 engine rpm but the cost of the engine is more and the torque is less (44.7 Nm @ 11750 engine rpm) as compared to the F4i.

3) Ergonomics

An ergonomic set-up was designed for two purposes:

1) To reduce driver fatigue by selecting an ergonomic position

2) To find the forces which the driver can apply

Each drivers' inputs have been considered and a position comfortable to each driver has been selected. These values acted as an input for designing the cockpit, pedal box, shifter system, seat and steering system. We also consulted a musculoskeletal specialist who helped us select the position in which the driver can apply maximum force with ease.

System Goal

Electronics

The goal for the electronics team this year is to design, build and implement an efficient electronics system which not only ensures higher reliability but also aides in vehicle analysis and tuning. The MoTec M400 ECU is selected over the Stock ECU based on its availability of features like launch and traction control, gear change ignition cut, the use of closed loop lambda control for dynamic fuel saving and one of the best GUI available for easy tuning.

The centralised telemetry system is self-designed to provide a wireless communication at 60MB/s over a range of 1 km and unlimited logging using a video capture system. The MoTec M400 data logging system is used to log sensor data at 200 Hz and i2 Standard is used to analyse the data. A sensor hub is made to provide plug and play of 14 sensor logging.

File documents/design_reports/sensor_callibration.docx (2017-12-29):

Chapter 5

Sensors and Calibration

List Of Sensors on the car:

- Accelerometer

- Air temperature sensor

- Brake pressure

- Engine temperature

- Exhaust gas temperature

- Fuel pressure sensor

- Lambda sensor

- Magnetic Sensor

- Oil pressure sensor

- Shock Travel Sensor

- Throttle position sensor

- Tire temperature

- Wheel Speed sensor

1. Accelerometer (Capacitive 3 - axis):

By virtue of its dimensions, characteristics and compatibility with gyroscopes, this 3 axis accelerometer allows the dynamic behaviour of the vehicle to be interpreted and checked.

The temperature compensation between - 20°C and 100°C allows the accelerometer to be used in extreme conditions.

This capacitive type 3 axis accelerometer, with a frequency range of up to 100 Hz, allows measurement of the acceleration of the constituent parts of the vehicle. The measuring range is from -5g to +5g.

Fig 5.1.a

3-axis Accelerometer

Calibration:


Fig 5.1.b

Longitudinal G Force Calibration


Fig 5.1.c

Vertical G Force Calibration


Fig 5.1.d

Lateral G Force Calibration

Logged Data:


Fig 5.1.e

Lateral & longitudinal G logged data

2. Air Temperature Sensor:

Air temperature sensor is a part of the AIE (air intake & exhaust) system on a car and is used to convert the engine intake air temperature into a voltage, which it then inputs into the engine control unit (ECU).

The engine control unit then uses this data to correct the rate of fuel injection to ensure the optimal use of fuel.

Fig 5.2.a

Inlet Air Temperature Sensor

Calibration:


Fig 5.2.b

Air Temperature Sensor calibration table

Logged Data:


Fig 5.2.c

Air Temperature Sensor logged data

3. Fluid Pressure Sensor (Brake/Fuel/Oil):

The pressure sensor gives voltage change with a change in fluid pressure. This sensor is used a brake pressure sensor, fuel pressure sensor and oil pressure sensor. The sensor used for different purposes is calibrated in the ECU.

Fig 5.3.a

Pressure Sensor

Calibration:


Fig 5.3.b

Brake Pressure Calibration


Fig 5.3.c

Fuel Pressure Calibration


Fig 5.3.d

Oil Pressure Calibration

Logged Data:


Fig 5.3.e

Brake Pressure Sensor logged data


Fig 5.3.f

Fuel Pressure Sensor logged data


Fig 5.3.g

Oil Pressure logged data

4. Engine Temperature Sensor:

An Engine Temperature Sensor (ETS) is a sensor that is screwed into the engine's block or cylinder head and is used to determine the temperature of the engine coolant. The sensor is basically a thermistor that changes resistance with temperature.

When the ETS is high (hotter), the resistance is low, and when the ETS is low (cooler) the resistance is high. This resistance reading is sent to the vehicle's ECU and can be used to activate emission controls or turn the engine's cooling fan on. The ETS sensor is usually a two wire sensor that uses a 5 volt reference from the ECU with a ground signal back to the ECU.

Fig 5.4.a

Engine Temperature Sensor

Calibration:


Fig 5.4.b

Engine Temperature Sensor Calibration

Logged Data:

Fig 5.4.c

Engine Temperature logged data

5. Exhaust Gas Temperature:

EGTs are resistance sensors whose resistance changes with change in temperature.

The resistance change cause voltage change and this voltage is calibrated in terms of temperature.


Fig 5.5.a

Exhaust Gas Temperature Sensor

Calibration:


Fig 5.5.b

EGT Calibration

Logged Data:


Fig 5.5.c

EGT logged data

6. Lambda Sensor:

A lambda sensor is an electronic device that measures the proportion of oxygen (O2) in the liquid being analysed. It is generally used for Air Fuel Ratio measurement, which may be used for data logging or closed loop control of the Air Fuel Ratio.


Fig 5.6.a

Lambda Sensor

Logged Data:


Fig 5.6.b

Lambda Sensor logged data

7. Magnetic Sensor:

The Main Engine Sensors are required for correct operation of the ECU.

The engine RPM is derived from the REF trigger sensor.

The SYNC trigger sensor is required to synchronise the Fuel and Ignition to

the correct engine cycle for sequential injection and correct firing of multicoil

ignition systems.


Fig 5.7.a

Ref & Sync Capture

8. STS (Shock Travel Sensor):

Shock travel sensors are linear potentiometers with very high sensitivity and accuracy. The shock is measured by the change in voltage produced by the sensor.


Fig 5.8.a

Shock Travel Sensor

Calibration:


Fig 5.8.b

STS Calibration

Logged Data:

Fig 5.8.c

STS logged data

9. Throttle Position Sensor (TPS):

A throttle position sensor is used to monitor the position of the throttle in the car. The throttle position sensor acts as a load efficiency point for fuel map tuning.

Fig 5.9.a

Throttle Position Sensor

10. Tire Temperature sensor:

In order to measure the temperature of the surface of the tire, without affecting the tire, a non‐contact temperature sensor was needed. Many tire temperature sensor arrays are available commercially, which are designed for use with commercial Data Acquisition systems, costing over 200 dollars per sensor. A more cost effective solution was found from Melexis. The MLX90614 infrared temperature sensor has a built in 16‐bit ADC, in a package that is less than 10 mm in diameter. The standard model measures surface temperatures in a 90 degree cone emanating from its center. By placing the sensors approximately 1.5 to 2 inches away from the surface of the tire, three MLX90614 sensors can be aimed at the surface of the tire with no overlap in order to measure the temperature in three radial bands around the inside, middle, and outside of the tire surface.

The MLX90614 an I2C interface to communicate with the microcontroller. This method of interface requires only two wires in addition to the power and ground wires for the sensor. Additionally, the two communication wires are common to all sensors on the I2C bus, which allows the sensors to be daisy chained in line, whereas the SPI interface on the MCP320X ADC chips requires a chip select signal unique to each chip in addition to its 3 common communication lines. The MLX90614 is precise to ±0.02 Celsius, which is more than necessary for noting the difference in temperature on the tire.

Fig 5.10.a

Tire Temperature Sensor

Calibration:

The MLX90614 infrared temperature sensors report their values in a 16‐bit unsigned value. Each tick here is the equivalent of 0.02 Kelvin. In order to scale the value from the raw data form into Celsius degrees the following operation is performed:

Temperature Sensor scaling calculation

[(unsigned reading) ∗ 0.02] − 272.0 = Celsius degrees

This allows the temperature gradient across the tire to be easily seen as differences as slight at 0.02 degrees Celsius are recorded.

Logged Data:


Fig 5.10.2

Tire Temperature Logged Data

11. Wheel Speed Sensor:

A wheel speed sensor or vehicle speed sensor (VSS) is a type of tachometer. These sensors are mounted 1.5mm away from the tires to monitor the wheel speed.

Fig 5.11.a

Wheel Speed Sensor

Calibration:


Fig 5.11.b

Wheel Speed sensor calibration

Logged Data:


Fig 5.11.c

Wheel Speed sensor logged data

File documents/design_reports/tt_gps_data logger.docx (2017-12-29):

CHAPTER 3: TIRE TEMPERATURE AND GPS DATA LOGGER

System Goal

System Need

When suspension parameters were initially discussed, instantaneous measurements of camber was discussed. There was no way to package a system of sensors to measure camber in relation to the track without having a major impact on the dynamics of the suspension due to increased un-sprung weight or hanging off the sides of the car which could potentially clip cones at an auto‐cross course. Instead, a method to validate if a current camber setting was desired. As a car turns, the outside wheel is loaded, and the tire sidewalls flex, effectively pulling the contact patch of the tire under the car, causing more work to be done on the outside edge of the tire if the car was not set up with enough negative camber. With the increase in friction, the surface temperature of that area of the tire increases proportionally. Ideally, the contact patch of the tire would be flat at the most extreme lateral acceleration to get the most grip possible out of the tire. This would cause an even temperature across the entire width of the tire.

Fig 3.1

MLX90614 Infrared Temperature Sensor

System Design

In order to measure the temperature of the surface of the tire, without affecting the tire, a non‐contact temperature sensor was needed. Many tire temperature sensor arrays are available commercially, which are designed for use with commercial Data Acquisition systems, costing over 200 dollars per sensor. A more cost effective solution was found from Melexis. The MLX90614 infrared temperature sensor has a built in 16‐bit ADC, in a package that is less than 10 mm in diameter. The standard model measures surface temperatures in a 90 degree cone emanating from its center. By placing the sensors approximately 1.5 to 2 inches away from the surface of the tire, three MLX90614 sensors can be aimed at the surface of the tire with no overlap in order to measure the temperature in three radial bands around the inside, middle, and outside of the tire surface.

The MLX90614 an I2C interface to communicate with the microcontroller. This method of interface requires only two wires in addition to the power and ground wires for the sensor. Additionally, the two communication wires are common to all sensors on the I2C bus, which allows the sensors to be daisy chained in line, whereas the SPI interface on the MCP320X ADC chips requires a chip select signal unique to each chip in addition to its 3 common communication lines. The MLX90614 is precise to ±0.02 Celsius, which is more than necessary for noting the difference in temperature on the tire.

Programming protocol

MLX90614 Infrared Temperature Sensor

The MLX90614 infrared temperature sensors report their values in a 16‐bit unsigned value. Each tick here is the equivalent of 0.02 Kelvin. In order to scale the value from the raw data form into Celsius degrees the following operation is performed:

Temperature Sensor scaling calculation

[(unsigned reading) ∗ 0.02] − 272.0 = Celsius degrees

This allows the temperature gradient across the tire to be easily seen as differences as slight at 0.02 degrees Celsius are recorded.

The major trouble with working with multiples of the MLX90614 is the communication. This unit uses an I2C communication protocol. I2C is a very common and very useful protocol as it uses only 2 wires in addition to the power and ground for the chip it is connecting to, as opposed to 4 wires for SPI. However, since I2C does not have a chip select function, every I2C device has a Slave Address set in its EEPROM (Electronically Erasable Programmable Read Only Memory), and in the case of the MLX90614 and most I2C devices, it is set to a default value from the factory. In order to change the slave address of the sensor, it must be first reset to 0x000 (0 in hexadecimal, representing 12 zeros in binary) and then set to the desired new address. The MLX90614 must then be power cycled for the new address to take effect. This process may seem simple, however, in order to write to the EEPROM in the MLX90614, a Cyclic Redundancy Check (CRC) is required. The CRC is an additional byte of data that is calculated based on the bytes preceding it in the packet. This is used to check for any sort of transmission error. The sensors were programmed to change their address. The addresses were from 0x01 to 0x0c and arranged accordingly on a breadboard.


Fig 3.1

Code

#include <i2cmaster.h>

void setup(){

Serial.begin(115200);

Serial.println("Setup...");

i2c_init(); //Initialise the i2c bus

PORTC = (1 << PORTC4) | (1 << PORTC5);//enable pullups

}

void loop(){

Serial.print("time:");

Serial.print(millis());

for(int i =1;i<13;i++)

{

int dev = i<<1;

int data_low = 0;

int data_high = 0;

int pec = 0;

i2c_start_wait(dev+I2C_WRITE);

i2c_write(0x07);

// read

i2c_rep_start(dev+I2C_READ);

data_low = i2c_readAck(); //Read 1 byte and then send ack

data_high = i2c_readAck(); //Read 1 byte and then send ack

pec = i2c_readNak();

i2c_stop();

//This converts high and low bytes together and processes temperature, MSB is a error bit and is ignored for temps

double tempFactor = 0.02; // 0.02 degrees per LSB (measurement resolution of the MLX90614)

double tempData = 0x0000; // zero out the data

int frac; // data past the decimal point

// This masks off the error bit of the high byte, then moves it left 8 bits and adds the low byte.

tempData = (double)(((data_high & 0x007F) << 8) + data_low);

tempData = (tempData * tempFactor)-0.01;

float celcius = tempData - 273.15;

// float fahrenheit = (celcius*1.8) + 32;

//Serial.println(i);

//Serial.print("time:");

// Serial.print('\t');

//Serial.print(millis());

Serial.print('\t');

//Serial.print("Celcius: ");

Serial.print(celcius);

Serial.print('\t');

//Serial.print("Fahrenheit: ");

//Serial.println(fahrenheit);

//delay(1000); // wait a second before printing again

}

Serial.println();

}

Hardware

Four PCBs for four tires were manufactured and the sensors were soldered according to their addresses. Four pin relimate connectors were used to connect the sensors from four PCBs to the data logger.

Tire Data Analysis


Fig 3.2

GPS

The GPS data logger wirelessly transmits the NMEA data to the computer. This data can be used to view live position of the car and get a trace of the entire lap. The GPS module works on UART. It sends out data serially which is read by the same data logger.

The data logger has an FTDI chip onboard which converts UART to USB so that the data can sent to the computer via the telemetry system which has USB ports on it.


Fig 3.3

Code

#include <SoftwareSerial.h>

#include <TinyGPS.h>

/* This sample code demonstrates the normal use of a TinyGPS object.

It requires the use of SoftwareSerial, and assumes that you have a

4800-baud serial GPS device hooked up on pins 3(rx) and 4(tx).

*/

TinyGPS gps;

SoftwareSerial ss(3, 4);

void setup()

{

Serial.begin(115200);

ss.begin(9600);

//Serial.print("Simple TinyGPS library v. "); Serial.println(TinyGPS::library_version());

//Serial.println("by Mikal Hart");

// Serial.println();

}

void loop()

{

bool newData = false;

//unsigned long chars;

//unsigned short sentences, failed;

// For one second we parse GPS data and report some key values

for (unsigned long start = millis(); millis() - start < 1000;)

{

while (ss.available())

{

char c = ss.read();

Serial.write(c); // uncomment this line if you want to see the GPS data flowing

//if (gps.encode(c)) // Did a new valid sentence come in?

//newData = true;

}

}

/*

if (newData)

{

float flat, flon;

unsigned long age;

gps.f_get_position(&flat, &flon, &age);

Serial.print("LAT=");

Serial.print(flat == TinyGPS::GPS_INVALID_F_ANGLE ? 0.0 : flat, 6);

Serial.print(" LON=");

Serial.print(flon == TinyGPS::GPS_INVALID_F_ANGLE ? 0.0 : flon, 6);

Serial.print(" SAT=");

Serial.print(gps.satellites() == TinyGPS::GPS_INVALID_SATELLITES ? 0 : gps.satellites());

Serial.print(" PREC=");

Serial.print(gps.hdop() == TinyGPS::GPS_INVALID_HDOP ? 0 : gps.hdop());

}

gps.stats(&chars, &sentences, &failed);

Serial.print(" CHARS=");

Serial.print(chars);

Serial.print(" SENTENCES=");

Serial.print(sentences);

Serial.print(" CSUM ERR=");

Serial.println(failed);

*/}

DATA LOGGER

The data logger uses AVR Atmega328 the schematic for the PCB was referred from arduino.cc. The arduino IDE was used for coding purpose. To log the data on a micro SD card a PCB was required with an SD card socket on it. Since the manufacturing cost of a new PCB for SD card was same as that available from sparkfun we decided to buy the PCB from sparkfun.com. This PCB also had enough space to accommodate the GPS module on it.

The tire temperature harness had relimte connectors at both the ends connecting the tire temperature sensor PCBs and the data logger.


Fig 3.4


Fig 3.5

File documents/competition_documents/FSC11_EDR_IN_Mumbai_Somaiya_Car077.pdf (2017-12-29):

Orion Racing India has been participating in Formula Student for the past 4 years. This year our major technical aims were extensive usage of composite materials, improved driver ergonomics and making the car extremely robust and reliable. Composite Systems was introduced as new entity to facilitate further research.

Chassis –
The Aeton car is made of tubular Steel space frame. The material used is AISI 1020 cold rolled Seamless tubes of diameter 25.4mm and variable wall thickness varying from 2.4mm to 1.25mm. The Welding used is CO2 welding. We designed the chassis for a Torsional Rigidity of 2000 N/m. Ergonomic considerations were taken using a wooden dummy. Steel fixtures were employed to ensure precision during manufacturing. Also the engine bay has been designed to remove the engine from the top easily.

Suspension –
Suspension geometry was designed for a 270kg vehicle with a 70kg driver and 45% front and 55% rear static weight distribution. We have designed an aspect ratio of 0.848 and the front and rear wheel frequencies have been set to 2.2 Hz and 2.0 Hz respectively for smaller front amplitude of vibration to enable driver visibility and control. Front geometry brake anti-dive is at 14.4%. We have increased the geometric roll centre’s height from the ground, thus decreasing the moment arm length between the vehicle's theoretical centre of mass and the geometrical roll centre. An additional design consideration for this was for the increase in the height of the lowest member of the nose resulting in an increase in elevation in the cockpit's floor to aid ergonomics. The shock-absorbers have been mounted inboard actuated by pushrods in the same transverse plane. Steel wishbones and aluminium bellcranks and uprights with hard-anodizing and EN-47 spring steel anti-roll bars comprise the system.

Steering –
The major goal set this year was to reduce the steering effort to aid the driver. We also designed a new custom wheel since the previous wheel was very small. Analysing tire data, we calculated the maximum slip angles on basis of speed and testing results. We selected a 100% static Ackermann to 76% dynamic Ackermann due to excessive tire wear and the slip angles being considered for maximum case only. Ackermann geometry also gave us better turning radius at lower speeds. We are running a rack and pinion due to easy manufacturability and ease of the system. The column is manufactured out of EN31 since gear cutting was easy on it and it is also stronger than EN24 or EN8. We have used two bearings to support the shaft and to stop misalignment at both wheel end and gear end. The tie rod point on the upright is also bolted on to give variable geometry. The toe is point is behind the upright to distribute the load on the upright coming from the calipers and it also moves the rack towards the Front Roll hoop eliminating template problems.

Brakes –
The brake pedal is designed to withstand 2000N of foot force as per the new rule. Considering the dynamic change in bias, the brake pedal is kept tilted towards the driver side. The brake rotors of 220mm (front) and 218.5mm (rear) and master cylinder bore diameter of 0.625 inch (front) and 0.7 inch (rear) were selected to provide natural bias. Al-2014 was selected as the material for front hubs for its high yield strength, good fatigue properties and easy machinability.EN-24 spring steel was selected for rear hubs as it was designed to mate with the splined axles of EN-24 material. For the ease of routing the accelerator cable was routed using a 90 degree spherical ball joint. Also tension springs were replaced by torsion springs to prevent interference of the driver’s foot while operating the pedals with mount of tension springs. Hubs were designed to facilitate the easy removal of brake rotors from the outboard side without disassembling the wheel assembly.

Powertrain –
The primary objective of the powertrain was to provide for a reliable engine package with a properly tuned engine and a dry sump lubrication system to overcome the starvation issues. Unfortunately due to time constraints we could not put the dry sump system onto the car but it has been completely designed and tested on the last year’s car. The components designed were Oil reservoir, pressure relief valve housing and flat oil pan. As the stock pressure relief valve wouldn’t fit inside because of the flat oil pan we had to design a housing so that the relief valve would fit into the main oil gallery and maintain oil pressure. The material used was Al 6351. We tilted the engine for a flat oil pan for ease of manufacturing. The co-ordinates of the stock oil sump were recorded using a CMM which were then put onto CAD to design the pan. A thermal load analysis was done on the oil pan to check for warping under high temperature. The material used was Al 6061.

Air Intake and Exhaust –
Our major goal for the air intake system was to reduce the weight of the by 25%. To achieve this, we manufactured the airbox using rapid prototyping (SLS). The material selected was Duraform PA due to better stress capacities. A layer of epoxy resin was also coated to make the airbox stronger. Also, the restrictor has been made completely of carbon fibre. For the airbox, we made use of the kinetic energy conservation, rolling flow plenum design, incorporating a diffusing section at the inlet to increase airflow to the extreme left and right cylinders. Inlet velocity for the airbox at peak suction pressure was calculated to be 433.59m/s. The exhaust system was made using mild steel and was then coated with a heat resistant ceramic coat. A 4-2-1 header design was preferred over the 4-1 header design so as to increase mid-range performance. Both, the intake and the exhaust system have been designed for an engine speed range of 8,500 to 10,500 rpm. The injector seats and offset adaptors have been machined from a single piece of Aluminium. The airbox is mounted towards the main roll hoop to avoid template problems.

Cooling –
The major goal of the cooling system was to design a reliable cooling system which would give variable heat rejection rate by controlling the flow rate of electric water pump. We have employed NTU method for heat rejection calculations. The stock cooling pump on Honda CBR600 F4i varies its flow rate according to the engine RPM, thus the cooling system will not operate when the engine is stalled. Hence we have used Davies Craig EWP80 electric pump which gives flow rate depending on the amount of voltage supplied to it. We have also used Davies Craig 8" thermatic fan instead of stock fan, the main reason being weight. We tested the flow rate of pump at 12V DC to be 75 LPM which is within the limits of manufacturer's claim. We also tested the free stream velocity of air by our fan to be 7.5 m/s. For calculations for radiator size were done for 70LPM water side flow rate and 5m/s velocity accounting for water side and air side losses. The radiator is fabricated out of aluminium due to its light weight and good thermal conductivity. We have also taken in consideration the proper placing of radiator so that the natural air flow is perpendicular to the radiator. The side pod incorporating the radiator is of diverging-converging section to achieve good air convection and good pressure drops.

Drivetrain –
The design was with the goal of improving the drive ability of the car and the reliability of the system. We have used a Salisbury Differential since it gives different settings of Torque Bias Ratios to choose from and for its better tuning options. The Differential has been mounted to facilitate easy assembly and can accommodate different sizes of sprockets easily by varying the length of the shackle plates that support the light weight aluminum differential mounts to chassis from one end which can be substituted for turnbuckles for fine tuning. A 520 chain has been used instead of the 525 chain that has been used for the past years. An Aluminum Driven Sprocket and an Integrated Tripod joint with Stub Axle to transmit drive from the differential have been designed and successfully implemented. Rear Hub assembly was designed in such a way that it is very convenient for the assembly and disassembly of the driveshafts without having to disturb the suspension system. The rear hub is driven by a tripod joint which drives a half shaft inserted into the hub from the outside the hub assembly. If the shaft is removed outwards then the outboard tripod will be disconnected and entire driveshaft assembly is easily removed. To prevent accidental removal of the half shaft a back plate is bolted to the hub on the outer side so that the half shaft does not come out.

Electronics –
The main aim this year was to make a robust and reliable electronics system which aids vehicle analysis and quick troubleshooting.
Design Process: Proteus Simulation-Breadboard Testing- Rough
implementation- Final implementation. This helped to identify many redundant circuits. All units except the ECU were designed and developed In-House.

Design Process: Proteus Simulation-Breadboard Testing- Rough
implementation- Final implementation. This helped to identify many redundant circuits. All units except the ECU were designed and developed In-House. Data Acquisition System is built around a dsPIC33FJ128GP706A controller., logging the data into a USB flash drive. It can log data at a much higher rate than a SD card which we were using until last year. This system can take inputs from 18 sensors. We also have a GPS system with a higher update rate (4Hz) and capable of logging data independently. This year we have also developed a telemetry system which we use to monitor the car while it is running. We have also developed a LCD system for the driver to view certain parameters of the car. The LCD system can communicate with the data acquisition system over the CAN bus.

Composites –
The Aeton’s Impact attenuator is made up of prepreg carbon fibre. It has increasing layers towards the base to reduce the G levels and increasing the energy absorbing capacity. Beta foam block filled on the inside is used as the damping element. The Energy absorbing capacity of the attenuator is 16000J. It weighs 550gms with peak deceleration and average deceleration of 19.5G and 9.5G respectively. Prepreg carbon fibre (twill weave,300gsm) with the following orientation: 0-30mm (0/90 +-45 0/90) , 30-140mm (0/90 0/90 +-45 0/90), 140-205mm (0/90 0/90 +-45 0/90 0/90 0/90) , 205-265mm (0/90 0/90 0/90 +-45 0/90 0/90 0/90) was laminated on the epoxy tooling block(male pattern).The part was then vacuum bagged and then cured at 120o C at 8bar pressure for 7 hours. Final pattern was released directly from the pattern to reduce the mould making cost. Carbon fibre (200gsm, 2k, simple weave), glass fibre(460gsm, simple weave) and epoxy resin LY556 with Aradur 991 hardener is used to make the nose, side pods, rear cover, seat and other mounts of the car. The nose and the rear cover of the car is made of 1 layer carbon fibre (200 gsm) and 1 layer glass fibre (400gsm). The nose weighs 1.76 kgs, 400gms lighter as compared to our last year’s nose. The rear cover weighs 860gms. The reason for using glass fibre was to add stiffness to the carbon fibre. To reduce mould making cost, we have identical side pods and we could get both the side pods from a single mould only. The side pods and the seat were made of 3 layers of carbon fibre. The side pods weigh 1.19kgs, 330 gms lighter than last year’s. The seat weighs 1.2 kgs. Structural foam and chopped strand glass fibre were used as the pattern and mould making materials respectively. The full bodyworks weighs 8.7kgs 39.5% lighter as compared to our last year’s bodywork which weighed 14.2 kgs. We also have a Carbon Fibre and Aluminium sandwiched steering wheel which we are still testing. We have also made a prototype air box out of carbon fibre and are now investing time into a composite fuel tank.

Miscellaneous –
We have implemented a fully electronic solenoid shifter because it is much reliable and faster than a hand shifter. It also let us invest some time into Gear change ignition cut to reduce jerks during shifting and a hand clutch, however it is still in the testing phase and has not been implemented on the car fully.

### Acceleration Vs Time Plot

Acceleration, g; Time, s; Disc – PCD 218.5mm; Half Shaft Locking Pin; Tripod Housing; Caliper; Taper Roller Bearing – SKF 32007; Upright; Single Flange Wheel Hub

Splined Half Shaft
to hold tripod
housing


1260 mm

1250 mm


1580 mm

1340 mm

2837 mm


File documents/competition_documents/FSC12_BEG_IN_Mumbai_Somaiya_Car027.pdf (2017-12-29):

TEAM - ORION RACING INDIA | CAR No. 27

# Electronics

DATA ACQUISITION SYSTEM


The Data Acquisition System is a self-designed system that logs data for 18 sensors. It uses its own battery and is independent from the car. The data is logged through analog channels and then converted into digital data using the internal 12 bit ADC of the microcontroller. The sensor is then calibrated using equations which are acquired through Matlab. The resolution is 0.8mV. The sensor readings are logged into USB through V-drive 2 in “.xls” format which can be easily viewed on Microsoft Excel. The logging rate for the USB is 25 Hz. The data is also logged live through telemetry using X-bee. The data is read through HyperTerminal. The outdoor RF line of sight range of transmission is 1600m and urban range is up to 90m.

DRIVER INTERFACE

The LCD System was designed using a pic18f controller board. The system has 4 line system and we used the internal EEPROM the LCD board to design a 3 line gear positioning system. The system also displays speed, odometer, lap distance, battery voltage sensor and engine temperature. This controller has a 13 channel ADC interfacing with a single multiplexed ADC module working at 100ns. This module has four 8/16 bit timers for speed calculation. Every sensor has been calibrated using Matlab and guard bands have been created to prevent uncertainty within the controller.

TEAM - ORION RACING INDIA | CAR No. 27


RPM Shift Lights

RPM Shift Lights lets the driver know when to shift gear through the lighting of the LEDs giving him a rough idea of the engine rpm. The circuit was supposed to be small and have two parallel lines of LEDs so that they can be seen clearly by the driver.


The circuit consists of LM 3914 which is a bar/dot display driver. A maximum of 10 LEDs can be driven. The LEDs are driven according to the voltage variation at the signal pin of the IC which is pin no.5. The signal from the ECU for engine revolution was a varying frequency signal. We are using IC LM 2907 which is a frequency to voltage convertor. This IC converts the frequency from the signal and converts it into analog voltage at 1V/67Hz.

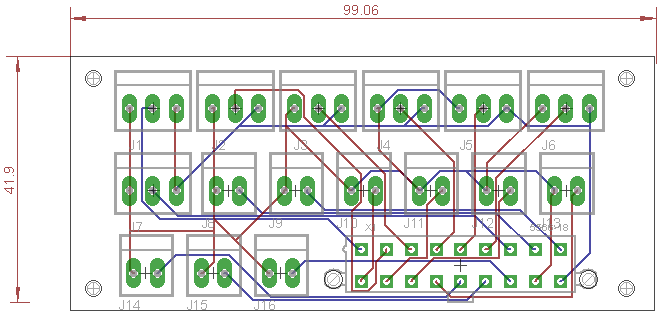
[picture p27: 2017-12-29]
schematics_images/sensor_hub/sensor hub.png

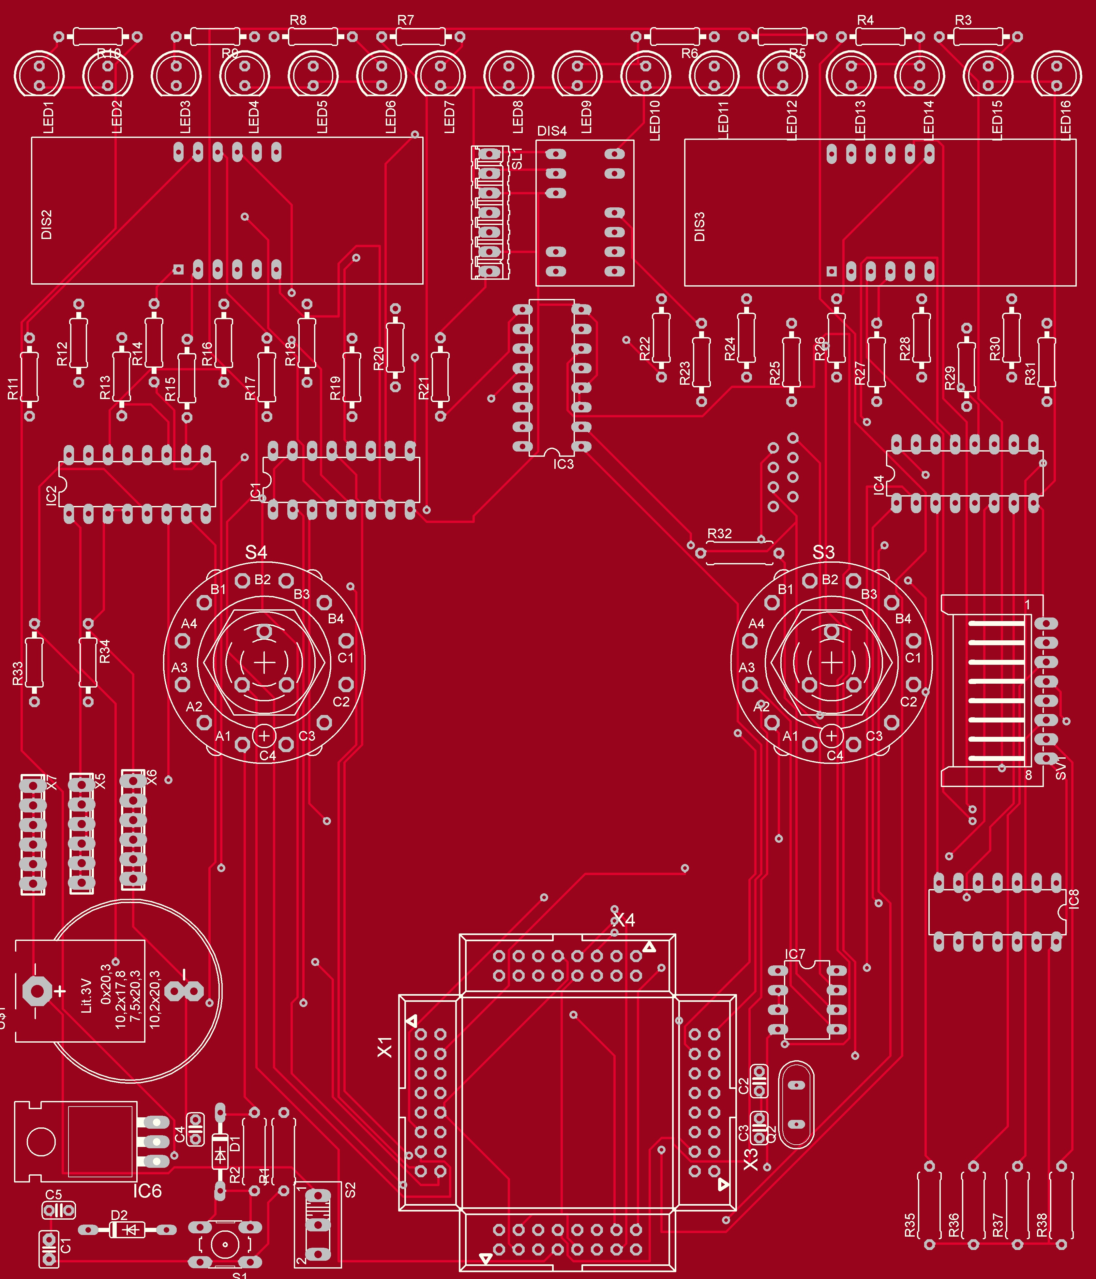
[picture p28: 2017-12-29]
schematics_images/driver_interface_system/eagleUp/asd.jpg

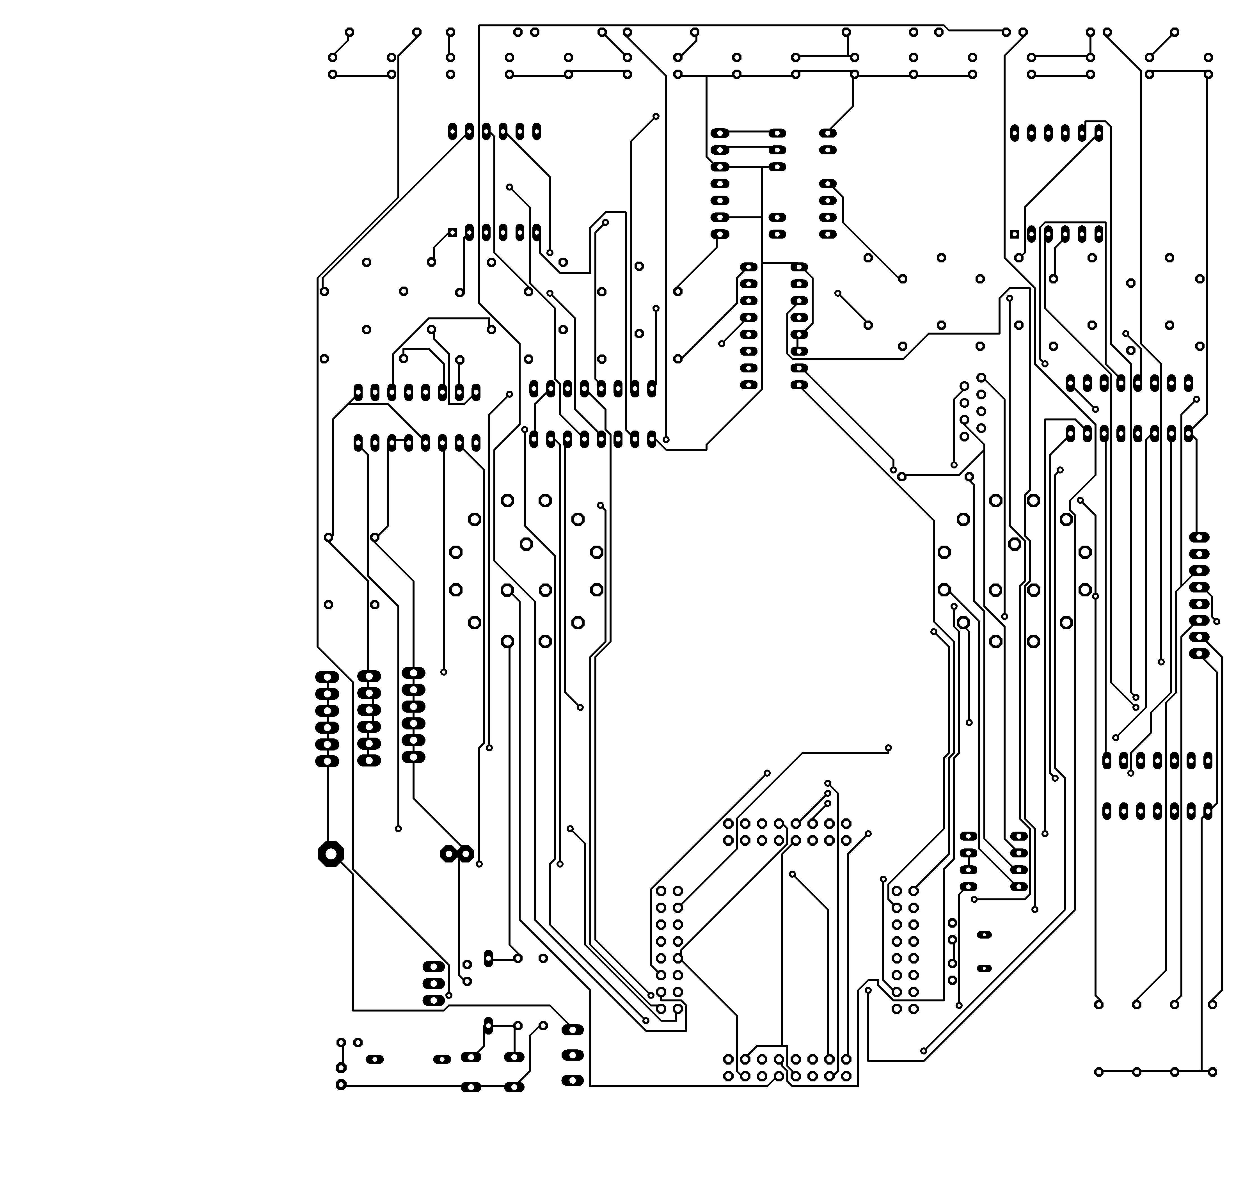
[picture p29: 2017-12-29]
schematics_images/driver_interface_system/eagleUp/eagleUp_display_top.png

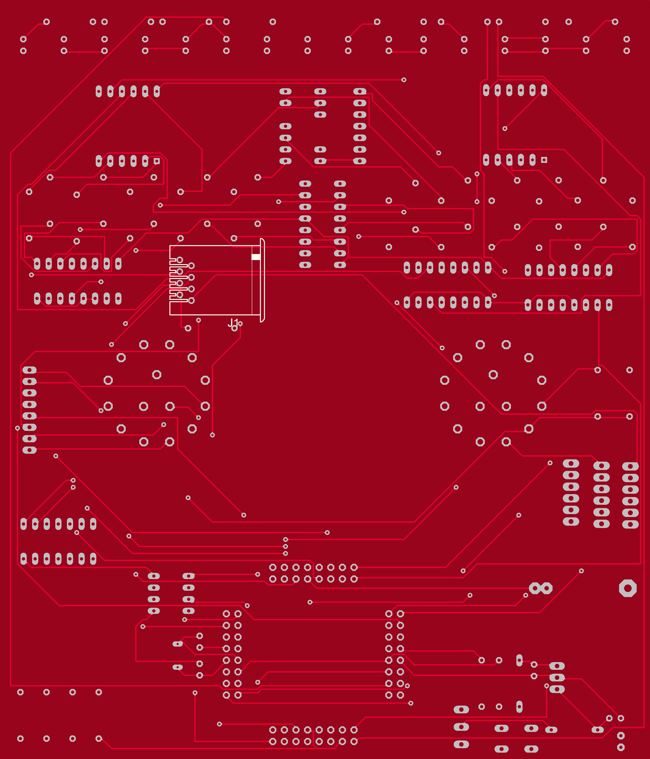
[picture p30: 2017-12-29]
schematics_images/driver_interface_system/eagleUp/eagleUp_display_board_bottom.png

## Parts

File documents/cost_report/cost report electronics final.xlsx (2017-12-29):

 |  | SYSTEMS AND INSTRUMENTS
ASSEMBLY: | CONTROL AND POWER WIRING |  |  |  |  | ASSEMBLY NO.
Materials | Type | Category | Cost/Unit | Unit 1 | Quantity | Cost
Connector, High Power, > 2 Amps | Any | Electronics | $2.00 | pin(s) | 2 | 4.00
Connector, Single Wire | Any | Electronics | $0.05 | wire | 9 | 0.45
Heat Shrink Tubing | Any | Electronics | $0.50 | m | 9.4 | 4.70
Lamp, LED | Any | Electronics | $0.50 | unit | 30 | 15.00
Motor, 12 Volt, DC Brush | Any | Electronics | $20.00 | unit |  | 0.00
Switch, Kill | Any | Electronics | $3.00 | unit | 2 | 6.00
Switch, Pushbutton | Any | Electronics | $1.00 | unit | 1 | 1.00
Switch, Toggle | Any | Electronics | $1.00 | unit | 1 | 1.00
Wire, Control | Any | Electronics | $1.00 | m | 13.64 | 13.64
Wire, Power | Any | Electronics | $3.00 | m | 12.9 | 38.70
 |  |  |  |  | TOTAL | 84.49
Processes | Type | Category | Cost/Unit | Unit 1 | Quantity | Cost
Attach Wire, Terminated wire with screw and nut | Electrical - Attach Wires | Electronics | £0.52 | unit | 4 | £2.08
Shrink Tube | Electrical - Bundle Processing | Electronics | £0.15 | cm | 940 | £141.00
Connector Install, Square, Latch/Snap-on Type | Electrical - Connections | Electronics | £0.17 | unit | 1 | £0.17
Crimp Wire | Electrical - Prep | Electronics | £0.17 | unit | 24 | £4.00
Cut wire | Electrical - Prep | Electronics | £0.08 | unit | 24 | £2.00
Strip Wire | Electrical - Prep | Electronics | £0.08 | unit | 24 | £2.00
 |  |  |  |  | TOTAL | £151.25
ASSEMBLY:ENGINE,DI,SENSORS |  |  |  |  |  | ASSEMBLY NO.
Materials | Type | Category | Cost/Unit | Unit 1 | Quantity | Cost
Connector, Computer Type | Any | Electronics | $1.00 | pin(s) | 8 | 8.00
Connector, OEM Quality | Any | Electronics | $0.50 | pin(s) | 35 | 17.50
Display, 7 Segment | Any | Electronics | $1.00 | digit | 9 | 9.00
Heat Shrink Tubing | Any | Electronics | $0.50 | m | 8.4 | 4.20
Lamp, LED | Any | Electronics | $0.50 | unit | 16 | 8.00
Switch, Rotary Multi-position Selector | Any | Electronics | $3.00 |  | 2 | 6.00
Wire, Signal | Any | Electronics | $1.00 | m | 31.7 | 31.70
Sensor, Accelerometer, 3 Axis | Any | Sensors | $8.00 | unit | 1 | 8.00
Sensor, Air Temperature | Any | Sensors | $4.00 | unit | 1 | 4.00
Sensor, Angular Position | Any | Sensors | $4.00 | unit | 2 | 8.00
Sensor, Fluid Pressure | Any | Sensors | $4.00 | unit | 2 | 8.00
Sensor, Hall Effect | Any | Sensors | $4.00 | unit | 4 | 16.00
Sensor, Manifold Absolute Pressure (MAP) | Any | Sensors | $4.00 | unit | 1 | 4.00
Sensor, Temperature | Any | Sensors | $8.00 | unit | 6 | 48.00
Sensor, Wide Band Air Fuel Raito | Any | Sensors | $35.00 | unit | 1 | 35.00
 |  |  |  |  | TOTAL | 215.40
Processes | Type | Category | Cost/Unit | Unit 1 | Quantity | Cost
Insert Bundle Into Tube or Sleeve | Electrical - Bundle Processing | Electronics | £0.02 | m | 31.7 | £0.63
Connector Install, Square, Latch/Snap-on Type | Electrical - Connections | Electronics | £0.17 | unit | 11 | £1.86
Lay Wire - Control | Electrical - Layout | Electronics | £0.02 | m | 31.7 | £0.63
Crimp Wire | Electrical - Prep | Electronics | £0.17 | unit | 59 | £10.03
Cut wire | Electrical - Prep | Electronics | £0.08 | unit | 59 | £4.92
Strip Wire | Electrical - Prep | Electronics | £0.08 | unit | 59 | £4.92
 |  |  |  |  | TOTAL | £22.99
ASSEMBLY:MOTEC HUB |  |  |  |  |  | ASSEMBLY NO.
Materials | Type | Category | Cost/Unit | Unit 1 | Quantity | Cost
Connector, High Power, > 2 Amps | Any | Electronics | 2 | pin(s) | 36 | 72
Heat Shrink Tubing | Any | Electronics | 0.5 | m | 0.5 | 0.25
Wire, Signal | Any | Electronics | 1 | m | 1.6 | 1.6
 |  |  |  |  | TOTAL | 73.85
Processes | Type | Category | Cost/Unit | Unit 1 | Quantity | Cost
Attach Wire, Wire to screw with nut | Electrical - Attach Wires | Electronics | £0.65 | unit | 4 | £2.58
Shrink Tube | Electrical - Bundle Processing | Electronics | £0.15 | cm | 6 | £0.90
Connector Install, Square, Latch/Snap-on Type | Electrical - Connections | Electronics | £0.17 | unit | 14 | £2.36
Lay Wire - Signal | Electrical - Layout | Electronics | £0.02 | m | 1.6 | £0.03
Crimp Wire | Electrical - Prep | Electronics | £0.17 | unit | 36 | £6.00
Cut wire | Electrical - Prep | Electronics | £0.08 | unit | 72 | £6.00
Strip Wire | Electrical - Prep | Electronics | £0.08 | unit | 72 | £6.00
 |  |  |  |  | TOTAL | £23.88
ASSEMBLY:CONTROL RELAYS |  |  |  |  |  | ASSEMBLY NO.
Materials | Type | Category | Cost/Unit | Unit 1 | Quantity | Cost
Connector, Computer Type | Any | Electronics | $1.00 | pin(s) | 8 | 8.00
Connector, Single Wire | Any | Electronics | $0.05 | wire | 6 | 0.30
Heat Shrink Tubing | Any | Electronics | $0.50 | m | 2.5 | 1.25
Relay, Control | Any | Electronics | $2.00 | unit | 3 | 6.00
Relay, Power | Any | Electronics | $4.00 | unit | 1 | 4.00
Terminal Block, Wiring | Any | Electronics | $0.25 | pin(s) | 3 | 0.75
Wire, Power | Any | Electronics | $3.00 | m | 0.25 | 0.75
Fuse, Control | Any | Electronics | $0.50 | unit | 3 | 1.50
Fuse, Power | Any | Electronics | $1.00 | unit | 1 | 1.00
Fuse, Signal | Any | Electronics | $0.50 | unit |  | 0.00
 |  |  |  |  | TOTAL | 23.55
Processes | Type | Category | Cost/Unit | Unit 1 | Quantity | Cost
Attach Wire, Wire to screw with nut | Electrical - Attach Wires | Electronics | £0.65 | unit | 7 | £4.52
Attach Wire, Wire to terminal block | Electrical - Attach Wires | Electronics | £0.35 | unit | 3 | £1.06
Shrink Tube | Electrical - Bundle Processing | Electronics | £0.15 | cm | 250 | £37.50
Connector Install, Square, Friction | Electrical - Connections | Electronics | £0.14 | unit | 4 | £0.56
Connector Install, Square, Latch/Snap-on Type | Electrical - Connections | Electronics | £0.17 | unit | 7 | £1.18
Lay Wire - Power | Electrical - Layout | Electronics | £0.03 | m | 3 | £0.09
Crimp Wire | Electrical - Prep | Electronics | £0.17 | unit | 12 | £2.00
Cut wire | Electrical - Prep | Electronics | £0.08 | unit | 12 | £1.00
Strip Wire | Electrical - Prep | Electronics | £0.08 | unit | 12 | £1.00
Ratchet <= 6.35 mm | Fasteners | Electronics | £0.50 | unit | 7 | £3.50
 |  |  |  |  | TOTAL | £52.41
ASSEMBLY:COOLING SYSTEM |  |  |  |  |  | ASSEMBLY NO.
Materials | Type | Category | Cost/Unit | Unit 1 | Quantity | Cost
Connector, OEM Quality | Any | Electronics | $0.50 | pin(s) | 2 | 1.00
Connector, Single Wire | Any | Electronics | $0.05 | wire | 2 | 0.10
Heat Shrink Tubing | Any | Electronics | $0.50 | m | 0.5 | 0.25
Wire, Power | Any | Electronics | $3.00 | m | 1.25 | 3.75
 |  |  |  |  | TOTAL | 5.10
Processes | Type | Category | Cost/Unit | Unit 1 | Quantity | Cost
Attach Wire, Terminated wire with screw and nut | Electrical - Attach Wires | Electronics | £0.52 | unit | 3 | £1.56
Connector Install, Square, Latch/Snap-on Type | Electrical - Connections | Electronics | £0.17 | unit | 1 | £0.17
Lay Wire - Power | Electrical - Layout | Electronics | £0.03 | m | 1.25 | £0.04
Crimp Wire | Electrical - Prep | Electronics | £0.17 | unit | 6 | £1.00
Cut wire | Electrical - Prep | Electronics | £0.08 | unit | 6 | £0.50
Strip Wire | Electrical - Prep | Electronics | £0.08 | unit | 6 | £0.50
 |  |  |  |  | TOTAL | £3.77

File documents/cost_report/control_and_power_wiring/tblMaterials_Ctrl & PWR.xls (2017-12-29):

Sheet: tblMaterials
Materials Table. Posted Version 14.0, 25-Apr-2012 |  |  |  |  |  |  |  |  |  |  | Added cost calculation
Material ID | Material | Supplier | Category | Table Price | Unit 1 | Numbers | Cost | Unit 2 | C1 | C2 | Size1 | Size2 | Calc Value | Modified | Comments
 | Battery, Advanced Chemistry (NiMH, Li-Ion, etc.) | Any | Electronics | $65.00 | kg | 1.5 | 97.50
 | Battery, Lead Acid | Any | Electronics | $3.00 | kg |  | 0.00
 | Circuit Breaker, Thermal, Klixon 7277-2-20 | Klixon | Electronics | $8.80 | unit |  | 0.00 |  |  |  |  |  |  | 2009-04-19
 | Connector, Aerospace Quality | Any | Electronics | $1.00 | pin(s) |  | 0.00
 | Connector, Computer Type | Any | Electronics | $1.00 | pin(s) |  | 0.00 |  |  |  |  |  |  |  | Seriel, Parallel, USB, Firewire, etc.
 | Connector, High Power, > 2 Amps | Any | Electronics | $2.00 | pin(s) | 2 | 4.00 |  |  |  |  |  |  |  | Vehicle power, starter, alternator, etc.
 | Connector, Single Wire | Any | Electronics | $0.05 | wire | 9 | 0.45 |  |  |  |  |  |  |  | Any style, any size, per wire end. Includes, ring, spade, bullet, etc.
 | Heat Shrink Tubing | Any | Electronics | $0.50 | m | 12.4 | 6.20
 | Lamp, LED | Any | Electronics | $0.50 | unit | 30 | 15.00
 | Motor, 12 Volt, DC Brush | Any | Electronics | $20.00 | unit |  | 0.00 |  |  |  |  |  |  |  | Used for general actuation. For more specefic motors please submit an Add Item RequeSteel
 | Switch, Kill | Any | Electronics | $3.00 | unit | 2 | 6.00
 | Switch, Pushbutton | Any | Electronics | $1.00 | unit | 1 | 1.00
 | Switch, Toggle | Any | Electronics | $1.00 | unit | 1 | 1.00
 | Wire, Control | Any | Electronics | $1.00 | m | 13.64 | 13.64
 | Wire, Power | Any | Electronics | $3.00 | m | 12.9 | 38.70
 |  |  |  |  |  |  | 183.49
 |  |  |  |  |  | processes | 196.2520833
 |  |  |  |  |  | total | 379.74

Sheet: Cross Reference List
Materials Cross Reference List Table. Commonly asked about items that do not appear in the table, or how to find them.
Material ID | Material | Modified | Cost As:
 | Brake Fluid | 2009-03-11 | Fluid, Oil
 | Differential Oil | 2009-03-11 | Fluid, Oil
 | Radiator Filler Knecks | 2009-03-11 | Cost as made
 | Radiator end caps | 2009-03-11 | Cost as made
 | Electrical components (resistors, capacitors, etc.) | 2009-03-11 | Chassis Control Module (by function)
 | Brake Hard Lines | 2009-03-11 | Cost from raw material (steel, aluminum, etc.) and include process operations to tubing ends
 | Coolant Hose | 2009-03-11 | Cost from raw material (rubber, silicone, etc.)
 | Radiator Hose | 2009-03-11 | Cost from raw material (rubber, silicone, etc.)

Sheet: EV
1. Introduction
The addition of the Electric vehicle category of cost components ugprdades the cost tables to now include fully parameterized costs for all components needed by electric vehicles. Thanks to the organizers of the Austrian and Australian competitions for the work that went into determining these costs.
2. Materials parameterization clarification
2.1. ECU, Rapid Prototyping
This covers the dSpace microAutoBox and similar systems from ETAS and other suppliers. Those Units are differentiated by their deigned targets being Lab cars, HIL systems and prototype vehicles.
2.2. ECU, Automotive
ECU designed for small- or large series application.
2.3. ECU, Industrial
Industrial Automation – type Control units, e.g. Siemens SiMatic and similar systems from B&R and other suppliers. If you have a full system with e.g. Inverter and control modules, you will need to cost both separately (see 2.5.10)
2.4. ECU, EV, student built
Use this item if you run your vehicle control (driver wish to motor torque request) on a self-designed unit, usually some kind of microcontroller + I/O. You will have to use the ECU add-ons (e.g. Traction Control) from the materials table if you have those features.
2.5. Chassis Control Modules
Since the System Topology of each EV will probably be different, we decided to stick to the Cost Committee recommendation to cost the EV function “boxes” as Chassis Control Module (CCM) functions. This allows for individual functionality “grouping”. For each “box” in your car you need “Chassis Control Module, Baseline Enclosure” and one or more of the functionalities from the EV table. The “baseline” CCM covers whatever Power supply, MCU, PCB, wiring etc. you have in your box.
2.5.1. Chassis Control Module, + Battery Management System
Use this instead of “Chassis Control Module, +Battery Charger”. Cost of this function is per “channel”. A channel is one “tap” into your battery pack, usually one for each cell in series. If your BMS manages a 12S1P pack, you will probably have 12 channels, if you have a 10S4P, it will probably have 10 channels (although it manages 40 cells!).
2.5.2. Chassis Control Module, + Isolation Monitoring Device
Your Bender ISO F1 or similar. See also 2.5.14
2.5.3. Chassis Control Module, + Power Distribution Module
Low voltage power switchbox. This covers “electronic fuse boxes” as well as devices that switch e.g. pumps and fans. Cost is per independently switchable output channel.
2.5.4. Chassis Control Module, + TSAL
Your tractive system active light as of FSE Rule 7.13. Covers any type, e.g. LED, strobe, regular bulbs. Includes cost for “blink” circuits but not for HV DC-DC converters described in 2.5.7
2.5.5. Chassis Control Module, + TSAS, buzzer
Your tractive system active sound as of FSE rule 7.18, if you use a piezo buzzer similar device.
2.5.6. Chassis Control Module, + TSAS, melody
Your tractive system active sound 7.18, if you use a speaker to play a melody, or a sound clip.
2.5.7. Chassis Control Module, + DCDC-Power (>1A) HV->LV
DC/DC switching type voltage converter to generate low voltage from the tractive system high voltage supply.
2.5.8. Chassis Control Module, + DCDC-Power LV->LV
DC/DC switching type voltage converter to generate a powerful low voltage supply from another low voltage, e.g. 24V or 48V control system supply from 12V. Not needed for low power sensor supplies.
2.5.9. Chassis Control Module, + Battery Charger HV
Battery charger for your HV Battery, if mounted on the car. Cost is per kW (rated) charging power
2.5.10. Chassis Control Module, + Motor Controller AC
Inverter for one AC drive motor. You will need one for every motor. Includes the cost for low capacity HV capacitors. The cost is per kW continuous power. If this figure is not available, use (peak power * 0.5)
2.5.11. Chassis Control Module, + Motor Controller DC
Controller for DC drive motors. Use one for each independently controllable motor. Includes the cost for low capacity HV capacitors. The cost is per kW continuous power. If this figure is not available, use (peak power * 0.5)
2.5.12. Chassis Control Module, + HV Insulation Relay
Single-line HV insulation relay. Does not include cost for the electronics to switch it on or off.
2.5.13. Chassis Control Module, + HV Precharge
Single HV precharge circuit, complete with low-power HV relay, power resistor(s) and wiring. If you have multiple precharge circuits in your car (e.g. multiple battery containments) you will need a matching number.
2.5.14. Chassis Control Module, + HV Housing
You will need to add this item to each CCM that has high voltage inside. This adjusts for the higher cost of insulation, shielding etc. on these modules. This includes wire glands fitted to the case. Note that the CCM costs do not include HV wiring leaving the module, this has to be costed separately as wiring + e.g. lugs.
2.5.15. Chassis Control Module, + HC-HV Fuse incl. Box
The high voltage fuse element includes fuse, fuse holder, cover, terminals.
2.6. Battery, Tractive Lithium
Tractive system battery. Cost is per kWh and includes the PCBs, rails or whatever you use to electrically connect the cells to a pack. Note that the battery containers, carrier, etc. has to be cost separately!
2.7. Motor, Tractive AC
Cost per kW continuous power. Use peak power * 0.5 if this figure is not available.
2.8. Motor, Tractive DC
Cost per kW continuous power. Use peak power * 0.5 if this figure is not available.
2.9. Wiring HV (> 12 mm²)
HV wiring, any style ((non) shielded, solid/stranded, etc..). Cost per mm² conductive cross section and meter length.
2.10. Conduit incl. Nuts, Elbows etc.
HV wiring conduit as required by FSE rule 7.11. Any type, color and diameter. Includes cost for small parts to connect the conduit, e.g. elbows, nuts, plastic glands etc.
2.11. Connector, HC-HV Lug Type
Single-wire lug type connector for HV wiring as described in 2.9. Any size and style.
2.12. Connector, HC-HV incl. Interlock
Insulated HV connector, any style, cost per HV Pin. Includes cost for small pilot/interlock/grounding pins and casing.
3. Electric vehicle cost model example
3.1. Abstract & Terminology
Here we will provide you with a simple example of how the tractive system of an electric vehicle could be costed using the provided table. Fig.1 shows the principal layout of that vehicle. Note that this vehicle may not fulfill the FSE rules!
3.2. Battery
The battery of this vehicle consists of 72x 45Ah Lithium Cells connected in series but split into 6 containers. The overall capacity is therefore 6 x 12 x 45Ah x 3,7V = 11,98 kWH which will cost $600/kWh x 11,98 kWh = $7188
3.3. Battery Management
Each one of the six battery containers has one BMS board inside, which monitors the 12 cells and therefore has 12 channels. In the cost report:
6x Chassis Control Module, baseline enclosure = 6 x $25
6x Chassis Control Module + Battery Management System (12 ch.) = $20 x 12 = 6x $240
3.4. Electronic Control Unit
The car uses a dSpace MicroAutoBox as ECU, which qualifies as a Rapid Prototyping System and will therefore cost $5000.
3.5. IMD and TSAL/TSAS
On this car the IMD is integrated with the HV relay and TSAL/TSAS driver into one device.
In the cost report, this would look like this
Chassis Control Module, baseline enclosure $25
Chassis Control Module, + IMD $300
Chassis Control Module + PDU (4ch.) $28 (3 for the relays, 1 for the TSAL+TSAS)
Chassis Control Module + TSAL $10
Chassis Control Module + TSAS, buzzer $5
Chassis Control Module + HV housing $25
3.6. Motors
The car has dual DC motors, which are rated at 20 kW continuous power each:
2x Motor, Tractive DC 20x $50 = $1000 2x $1000
3.7. Motor Controller
The car uses a two-channel DC power stage which is rated at 25kW continuous power per channel:
1x Chassis Control Module, baseline enclosure $25
2x Chassis Control Module, + Motor Controller DC 2x $562,5 (=25x $22,5)
1x Chassis Control Module + HV housing $25
3.8. PDU
The PDU is a stand-alone device acting as an electronic fuse box and providing the ECU, and 4 other systems with power
Chassis Control Module, baseline enclosure $25
Chassis Control Module, + PDU (5ch.) $35
3.9. LV-Battery
The LV Battery is a low-performance LiIon 13,2V pack weighing about 1,2 kg.
Battery, advanced Chemistry $65/kg * 1,2kg $78
3.10. HV Wiring & systems
The wiring is not explained here, the standard harness process applies. The battery containment houses the 6 battery packs as well as the precharge circuit and HV Fuse:
Chassis Control Module, baseline enclosure $25
Chassis Control Module, +HV Fuse $100
Chassis Control Module, + HV Precharge $50

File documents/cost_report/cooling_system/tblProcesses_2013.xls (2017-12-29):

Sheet: Sheet1
Process Table. Posted Version 7, 30-Mar-2012
Process ID | Process | Unit Cost | Unit | Category | numbers | cost | Tooling Required | Near Net Shape | Multiplier Type Used | Modified | Comments
 | Attach Wire, Terminated wire with screw and nut | $0.52 | unit | Electrical - Attach Wires | 3 | 1.5625
 | Connector Install, Square, Latch/Snap-on Type | $0.17 | unit | Electrical - Connections | 1 | 0.16875
 | Lay Wire - Power | $0.03 | m | Electrical - Layout | 1.25 | 0.0375 |  |  |  | 2009-01-25
 | Crimp Wire | $0.17 | unit | Electrical - Prep | 6 | 1
 | Cut wire | $0.08 | unit | Electrical - Prep | 6 | 0.5
 | Strip Wire | $0.08 | unit | Electrical - Prep | 6 | 0.5
 |  |  |  |  |  | 3.76875

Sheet: Sheet2
Brake Rotor | 10 | 31.41592654 | linear in
 | 0.25 | 4.71238898 | linear in
 |  | 36.12831552 | linear in
 |  | 91.76592141 | linear cm
 |  | 9.176592141

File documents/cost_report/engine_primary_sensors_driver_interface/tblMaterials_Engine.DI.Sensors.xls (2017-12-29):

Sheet: tblMaterials
Materials Table. Posted Version 14.0, 25-Apr-2012 |  |  |  |  |  |  |  |  |  |  | Added cost calculation
Material ID | Material | Supplier | Category | Table Price | Unit 1 | Numbers | Cost | Unit 2 | C1 | C2 | Size1 | Size2 | Calc Value | Modified | Comments
 | Connector, Computer Type | Any | Electronics | $1.00 | pin(s) | 8 | 8.00 |  | 2 |  |  |  |  |  | Seriel, Parallel, USB, Firewire, etc.
 | Connector, OEM Quality | Any | Electronics | $0.50 | pin(s) | 35 | 17.50 |  | 3
 | Display, 7 Segment | Any | Electronics | $1.00 | digit | 9 | 9.00 |  |  |  |  |  |  |  | Each digit can represent a single character alpha or numeric
 | Heat Shrink Tubing | Any | Electronics | $0.50 | m | 10.4 | 5.20
 | Lamp, LED | Any | Electronics | $0.50 | unit | 16 | 8.00
 | Switch, Rotary Multi-position Selector | Any | Electronics | $3.00 |  | 2 | 6.00
 | Wire, Signal | Any | Electronics | $1.00 | m | 31.7 | 31.70
 | Sensor, Accelerometer, 3 Axis | Any | Sensors | $8.00 | unit | 1 | 8.00
 | Sensor, Air Temperature | Any | Sensors | $4.00 | unit | 1 | 4.00 |  |  |  |  |  |  |  | OEM quality sensor
 | Sensor, Angular Position | Any | Sensors | $4.00 | unit | 2 | 8.00 |  |  |  |  |  |  |  | e.g. Throttle Position Sensor (TPS)
 | Sensor, Fluid Pressure | Any | Sensors | $4.00 | unit | 2 | 8.00
 | Sensor, Hall Effect | Any | Sensors | $4.00 | unit | 4 | 16.00 |  |  |  |  |  |  |  | e.g. Wheel Speed Sensor
 | Sensor, Manifold Absolute Pressure (MAP) | Any | Sensors | $4.00 | unit | 1 | 4.00 |  |  |  |  |  |  |  | OEM quality sensor
 | Sensor, Temperature | Any | Sensors | $8.00 | unit | 6 | 48.00 |  |  |  |  |  |  | 2009-05-10
 | Sensor, Wide Band Air Fuel Raito | Any | Sensors | $35.00 | unit | 1 | 35.00 |  |  |  |  |  |  |  | Output proportional to air fuel ratio
 |  |  |  |  |  |  | 181.90
 |  |  |  |  |  |  | 141.00
 |  |  |  |  |  |  | 178.9875833
 |  |  |  |  |  |  | 319.99

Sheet: Cross Reference List
Materials Cross Reference List Table. Commonly asked about items that do not appear in the table, or how to find them.
Material ID | Material | Modified | Cost As:
 | Brake Fluid | 2009-03-11 | Fluid, Oil
 | Differential Oil | 2009-03-11 | Fluid, Oil
 | Radiator Filler Knecks | 2009-03-11 | Cost as made
 | Radiator end caps | 2009-03-11 | Cost as made
 | Electrical components (resistors, capacitors, etc.) | 2009-03-11 | Chassis Control Module (by function)
 | Brake Hard Lines | 2009-03-11 | Cost from raw material (steel, aluminum, etc.) and include process operations to tubing ends
 | Coolant Hose | 2009-03-11 | Cost from raw material (rubber, silicone, etc.)
 | Radiator Hose | 2009-03-11 | Cost from raw material (rubber, silicone, etc.)

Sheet: EV
1. Introduction
The addition of the Electric vehicle category of cost components ugprdades the cost tables to now include fully parameterized costs for all components needed by electric vehicles. Thanks to the organizers of the Austrian and Australian competitions for the work that went into determining these costs.
2. Materials parameterization clarification
2.1. ECU, Rapid Prototyping
This covers the dSpace microAutoBox and similar systems from ETAS and other suppliers. Those Units are differentiated by their deigned targets being Lab cars, HIL systems and prototype vehicles.
2.2. ECU, Automotive
ECU designed for small- or large series application.
2.3. ECU, Industrial
Industrial Automation – type Control units, e.g. Siemens SiMatic and similar systems from B&R and other suppliers. If you have a full system with e.g. Inverter and control modules, you will need to cost both separately (see 2.5.10)
2.4. ECU, EV, student built
Use this item if you run your vehicle control (driver wish to motor torque request) on a self-designed unit, usually some kind of microcontroller + I/O. You will have to use the ECU add-ons (e.g. Traction Control) from the materials table if you have those features.
2.5. Chassis Control Modules
Since the System Topology of each EV will probably be different, we decided to stick to the Cost Committee recommendation to cost the EV function “boxes” as Chassis Control Module (CCM) functions. This allows for individual functionality “grouping”. For each “box” in your car you need “Chassis Control Module, Baseline Enclosure” and one or more of the functionalities from the EV table. The “baseline” CCM covers whatever Power supply, MCU, PCB, wiring etc. you have in your box.
2.5.1. Chassis Control Module, + Battery Management System
Use this instead of “Chassis Control Module, +Battery Charger”. Cost of this function is per “channel”. A channel is one “tap” into your battery pack, usually one for each cell in series. If your BMS manages a 12S1P pack, you will probably have 12 channels, if you have a 10S4P, it will probably have 10 channels (although it manages 40 cells!).
2.5.2. Chassis Control Module, + Isolation Monitoring Device
Your Bender ISO F1 or similar. See also 2.5.14
2.5.3. Chassis Control Module, + Power Distribution Module
Low voltage power switchbox. This covers “electronic fuse boxes” as well as devices that switch e.g. pumps and fans. Cost is per independently switchable output channel.
2.5.4. Chassis Control Module, + TSAL
Your tractive system active light as of FSE Rule 7.13. Covers any type, e.g. LED, strobe, regular bulbs. Includes cost for “blink” circuits but not for HV DC-DC converters described in 2.5.7
2.5.5. Chassis Control Module, + TSAS, buzzer
Your tractive system active sound as of FSE rule 7.18, if you use a piezo buzzer similar device.
2.5.6. Chassis Control Module, + TSAS, melody
Your tractive system active sound 7.18, if you use a speaker to play a melody, or a sound clip.
2.5.7. Chassis Control Module, + DCDC-Power (>1A) HV->LV
DC/DC switching type voltage converter to generate low voltage from the tractive system high voltage supply.
2.5.8. Chassis Control Module, + DCDC-Power LV->LV
DC/DC switching type voltage converter to generate a powerful low voltage supply from another low voltage, e.g. 24V or 48V control system supply from 12V. Not needed for low power sensor supplies.
2.5.9. Chassis Control Module, + Battery Charger HV
Battery charger for your HV Battery, if mounted on the car. Cost is per kW (rated) charging power
2.5.10. Chassis Control Module, + Motor Controller AC
Inverter for one AC drive motor. You will need one for every motor. Includes the cost for low capacity HV capacitors. The cost is per kW continuous power. If this figure is not available, use (peak power * 0.5)
2.5.11. Chassis Control Module, + Motor Controller DC
Controller for DC drive motors. Use one for each independently controllable motor. Includes the cost for low capacity HV capacitors. The cost is per kW continuous power. If this figure is not available, use (peak power * 0.5)
2.5.12. Chassis Control Module, + HV Insulation Relay
Single-line HV insulation relay. Does not include cost for the electronics to switch it on or off.
2.5.13. Chassis Control Module, + HV Precharge
Single HV precharge circuit, complete with low-power HV relay, power resistor(s) and wiring. If you have multiple precharge circuits in your car (e.g. multiple battery containments) you will need a matching number.
2.5.14. Chassis Control Module, + HV Housing
You will need to add this item to each CCM that has high voltage inside. This adjusts for the higher cost of insulation, shielding etc. on these modules. This includes wire glands fitted to the case. Note that the CCM costs do not include HV wiring leaving the module, this has to be costed separately as wiring + e.g. lugs.
2.5.15. Chassis Control Module, + HC-HV Fuse incl. Box
The high voltage fuse element includes fuse, fuse holder, cover, terminals.
2.6. Battery, Tractive Lithium
Tractive system battery. Cost is per kWh and includes the PCBs, rails or whatever you use to electrically connect the cells to a pack. Note that the battery containers, carrier, etc. has to be cost separately!
2.7. Motor, Tractive AC
Cost per kW continuous power. Use peak power * 0.5 if this figure is not available.
2.8. Motor, Tractive DC
Cost per kW continuous power. Use peak power * 0.5 if this figure is not available.
2.9. Wiring HV (> 12 mm²)
HV wiring, any style ((non) shielded, solid/stranded, etc..). Cost per mm² conductive cross section and meter length.
2.10. Conduit incl. Nuts, Elbows etc.
HV wiring conduit as required by FSE rule 7.11. Any type, color and diameter. Includes cost for small parts to connect the conduit, e.g. elbows, nuts, plastic glands etc.
2.11. Connector, HC-HV Lug Type
Single-wire lug type connector for HV wiring as described in 2.9. Any size and style.
2.12. Connector, HC-HV incl. Interlock
Insulated HV connector, any style, cost per HV Pin. Includes cost for small pilot/interlock/grounding pins and casing.
3. Electric vehicle cost model example
3.1. Abstract & Terminology
Here we will provide you with a simple example of how the tractive system of an electric vehicle could be costed using the provided table. Fig.1 shows the principal layout of that vehicle. Note that this vehicle may not fulfill the FSE rules!
3.2. Battery
The battery of this vehicle consists of 72x 45Ah Lithium Cells connected in series but split into 6 containers. The overall capacity is therefore 6 x 12 x 45Ah x 3,7V = 11,98 kWH which will cost $600/kWh x 11,98 kWh = $7188
3.3. Battery Management
Each one of the six battery containers has one BMS board inside, which monitors the 12 cells and therefore has 12 channels. In the cost report:
6x Chassis Control Module, baseline enclosure = 6 x $25
6x Chassis Control Module + Battery Management System (12 ch.) = $20 x 12 = 6x $240
3.4. Electronic Control Unit
The car uses a dSpace MicroAutoBox as ECU, which qualifies as a Rapid Prototyping System and will therefore cost $5000.
3.5. IMD and TSAL/TSAS
On this car the IMD is integrated with the HV relay and TSAL/TSAS driver into one device.
In the cost report, this would look like this
Chassis Control Module, baseline enclosure $25
Chassis Control Module, + IMD $300
Chassis Control Module + PDU (4ch.) $28 (3 for the relays, 1 for the TSAL+TSAS)
Chassis Control Module + TSAL $10
Chassis Control Module + TSAS, buzzer $5
Chassis Control Module + HV housing $25
3.6. Motors
The car has dual DC motors, which are rated at 20 kW continuous power each:
2x Motor, Tractive DC 20x $50 = $1000 2x $1000
3.7. Motor Controller
The car uses a two-channel DC power stage which is rated at 25kW continuous power per channel:
1x Chassis Control Module, baseline enclosure $25
2x Chassis Control Module, + Motor Controller DC 2x $562,5 (=25x $22,5)
1x Chassis Control Module + HV housing $25
3.8. PDU
The PDU is a stand-alone device acting as an electronic fuse box and providing the ECU, and 4 other systems with power
Chassis Control Module, baseline enclosure $25
Chassis Control Module, + PDU (5ch.) $35
3.9. LV-Battery
The LV Battery is a low-performance LiIon 13,2V pack weighing about 1,2 kg.
Battery, advanced Chemistry $65/kg * 1,2kg $78
3.10. HV Wiring & systems
The wiring is not explained here, the standard harness process applies. The battery containment houses the 6 battery packs as well as the precharge circuit and HV Fuse:
Chassis Control Module, baseline enclosure $25
Chassis Control Module, +HV Fuse $100
Chassis Control Module, + HV Precharge $50

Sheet: Processes
Process Table. Posted Version 7, 30-Mar-2012
Process ID | Process | Unit Cost | Unit | Category | numbers | cost | Tooling Required | Near Net Shape | Multiplier Type Used | Modified | Comments
 | None | $0.00
 | Die Casting | $4.00 | kg | Basic Forming |  | 0 | Yes | Yes
 | Investment Casting | $8.00 | kg | Basic Forming |  | 0 |  | Yes
 | Laser Powder Deposition | $330.00 | kg | Basic Forming |  | 0 |  | Yes
 | Plastic injection molding | $2.75 | kg | Basic Forming |  | 0 | Yes | Yes
 | Powder Metal Forming | $3.00 | kg | Basic Forming |  | 0 | Yes | Yes
 | Rapid Prototype - Stereo Lith. | $32.00 | kg | Basic Forming |  | 0 |  | Yes
 | Sand Casting | $3.00 | kg | Basic Forming |  | 0 | Yes
 | Vacuum Form | $10.00 | m^2 | Basic Forming |  | 0 | Yes |  |  | 2012-03-30
 | Exhaust System Ceramic Coating | $25.00 | m | Coating |  | 0 |  |  |  | 2009-02-24 | Linear distance of coating on exhaust header and tubing including all runners, etc. Material included.
 | Cure, Autoclave | $50.00 | m^2 | Composite |  | 0 | Yes |  |  |  | Includes all consumable materials and labor.
 | Cure, Oven | $20.00 | m^2 | Composite |  | 0 | Yes |  |  |  | Includes all consumable materials and labor.
 | Cure, Room Temperature | $10.00 | m^2 | Composite |  | 0 | Yes |  |  | 2009-02-24 | Includes all consumable materials and labor.
 | Lamination, Fillament Winding | $25.00 | kg | Composite |  | 0 |  |  |  | 2009-03-26 | Cost based on finished part mass of composite fibers and resin.
 | Lamination, Manual | $35.00 | m^2 | Composite |  | 0
 | Potting | $0.50 | cm | Composite |  | 0 |  |  |  | 2009-04-26 | Cost based on perimeter of insert. Includes potting compund material cost
 | Resin application, Infusion Molding | $2.50 | m^2 | Composite |  | 0
 | Resin application, Manual | $5.00 | m^2 | Composite |  | 0 |  |  |  |  | If prepreg composites are used do not included the resin application step.
 | Attach Wire, Fork | $0.25 | unit | Electrical - Attach Wires |  | 0
 | Attach Wire, Quick connect terminal | $0.10 | unit | Electrical - Attach Wires |  | 0
 | Attach Wire, Ring | $0.48 | unit | Electrical - Attach Wires |  | 0
 | Attach Wire, Solder wire, bent | $0.35 | unit | Electrical - Attach Wires |  | 0
 | Attach Wire, Solder wire, not bent | $0.52 | unit | Electrical - Attach Wires |  | 0
 | Attach Wire, Terminated wire with screw | $0.35 | unit | Electrical - Attach Wires |  | 0
 | Attach Wire, Terminated wire with screw and nut | $0.52 | unit | Electrical - Attach Wires |  | 0
 | Attach Wire, Wire to screw | $0.48 | unit | Electrical - Attach Wires |  | 0
 | Attach Wire, Wire to screw with nut | $0.65 | unit | Electrical - Attach Wires |  | 0
 | Attach Wire, Wire to terminal block | $0.35 | unit | Electrical - Attach Wires |  | 0
 | Attach Wire, Wire wrap around terminal post | $0.27 | unit | Electrical - Attach Wires |  | 0
 | Install Tie Wrap (Zip Tie, Cable Clamp) | $0.09 | unit | Electrical - Bundle Install |  | 0 |  |  |  | 2009-02-17
 | Wire Dressing (Install and route) | $1.00 | m | Electrical - Bundle Install |  | 0
 | Insert Bundle Into Tube or Sleeve | $0.02 | m | Electrical - Bundle Processing | 31.7 | 0.634 |  |  |  | 2009-01-24
 | Install Adhesive Cable Clamp | $0.19 | unit | Electrical - Bundle Processing |  | 0
 | Lace | $0.15 | unit | Electrical - Bundle Processing |  | 0
 | Shrink Tube | $0.15 | cm | Electrical - Bundle Processing | 317 | 47.55 |  |  |  | 2009-03-26
 | Taping Wire Bundle | $0.04 | cm | Electrical - Bundle Processing |  | 0 |  |  |  | 2009-03-26
 | Connector Install, Circular, Bayonet | $0.11 | unit | Electrical - Connections |  | 0
 | Connector Install, Circular, Friction | $0.14 | unit | Electrical - Connections |  | 0
 | Connector Install, Circular, Screw Thread | $0.24 | unit | Electrical - Connections |  | 0
 | Connector Install, Square, Friction | $0.14 | unit | Electrical - Connections |  | 0
 | Connector Install, Square, Latch/Snap-on Type | $0.17 | unit | Electrical - Connections | 11 | 1.85625
 | Connector Install, Square, Screw (x2) | $0.50 | unit | Electrical - Connections |  | 0
 | Connector Install, Square, Spring Clip | $0.20 | unit | Electrical - Connections |  | 0
 | Lay Wire - Control | $0.02 | m | Electrical - Layout | 31.7 | 0.634 |  |  |  | 2009-01-25
 | Lay Wire - Power | $0.03 | m | Electrical - Layout |  | 0 |  |  |  | 2009-01-25
 | Lay Wire - Signal | $0.02 | m | Electrical - Layout |  | 0 |  |  |  | 2009-01-25
 | Crimp Wire | $0.17 | unit | Electrical - Prep | 59 | 10.03
 | Cut wire | $0.08 | unit | Electrical - Prep | 59 | 4.916666667
 | Strip Multi-Conductor | $0.13 | wire(s) | Electrical - Prep |  | 0 |  |  |  | 2009-01-24
 | Strip Wire | $0.08 | unit | Electrical - Prep | 59 | 4.916666667
 | Tin Wire | $0.12 | unit | Electrical - Prep |  | 0
 | Connector Assembley, Crimp | $0.36 | contacts | Electrical - Wire in Connector |  | 0 |  |  |  | 2009-01-24
 | Connector Assembley, Solder | $0.24 | contacts | Electrical - Wire in Connector |  | 0 |  |  |  | 2009-01-24
 | Hand - Start Only | $0.12 | unit | Fasteners |  | 0
 | Hand, Loose <= 25.4 mm | $0.50 | unit | Fasteners |  | 0
 | Hand, Loose <= 6.35 mm | $0.25 | unit | Fasteners |  | 0
 | Hand, Loose > 25.4 mm | $0.75 | unit | Fasteners |  | 0
 | Hand, Tight <= 6.35 mm | $0.50 | unit | Fasteners |  | 0
 | Power Tool <= 25.4 mm | $0.25 | unit | Fasteners |  | 0 |  |  | Fastener Installation
 | Power Tool <= 6.35 mm | $0.25 | unit | Fasteners |  | 0 |  |  | Fastener Installation
 | Power Tool > 25.4 mm | $0.50 | unit | Fasteners |  | 0 |  |  | Fastener Installation
 | Ratchet <= 25.4 mm | $0.75 | unit | Fasteners |  | 0 |  |  | Fastener Installation
 | Ratchet <= 6.35 mm | $0.50 | unit | Fasteners |  | 0 |  |  | Fastener Installation
 | Ratchet > 25.4 mm | $1.50 | unit | Fasteners |  | 0 |  |  | Fastener Installation
 | Reaction Tool <= 25.4 mm | $0.25 | unit | Fasteners |  | 0
 | Reaction Tool <= 6.35 mm | $0.25 | unit | Fasteners |  | 0
 | Reaction Tool > 25.4 mm | $0.50 | unit | Fasteners |  | 0
 | Screwdriver < 1 Turn | $0.12 | unit | Fasteners |  | 0 |  |  | Fastener Installation
 | Screwdriver > 1 Turn | $0.50 | unit | Fasteners |  | 0 |  |  | Fastener Installation
 | Wrench <= 25.4 mm | $1.50 | unit | Fasteners |  | 0 |  |  | Fastener Installation
 | Wrench <= 6.35 mm | $1.00 | unit | Fasteners |  | 0 |  |  | Fastener Installation
 | Wrench > 25.4 mm | $2.00 | unit | Fasteners |  | 0 |  |  | Fastener Installation
 | Braze | $0.15 | cm | Joining |  | 0 | Yes |  |  | 2009-03-26
 | Sewing | $0.08 | cm | Joining |  | 0
 | Weld | $0.15 | cm | Joining |  | 0 | Yes |  |  | 2009-02-24
 | Adjustment - Misc. | $5.00 | unit | Labor |  | 0 |  |  |  |  | Chain tension, etc.
 | Aerosol Apply | $5.25 | m^2 | Labor |  | 0
 | Annodize | $0.00 | unit | Labor |  | 0 |  |  |  | 2009-02-25 | It is not necessary to include any cost for annodizing. Included for reference only.
 | Assemble, >20 kg, Interference | $5.62 | unit | Labor |  | 0 |  |  | Assembly
 | Assemble, >20 kg, Line-on-Line | $3.75 | unit | Labor |  | 0 |  |  | Assembly
 | Assemble, >20 kg, Loose | $1.88 | unit | Labor |  | 0 |  |  | Assembly
 | Assemble, 1 kg, Interference | $0.19 | unit | Labor |  | 0 |  |  | Assembly
 | Assemble, 1 kg, Line-on-Line | $0.12 | unit | Labor |  | 0 |  |  | Assembly
 | Assemble, 1 kg, Loose | $0.06 | unit | Labor |  | 0 |  |  | Assembly
 | Assemble, 10 kg, Interference | $1.88 | unit | Labor |  | 0 |  |  | Assembly
 | Assemble, 10 kg, Line-on-Line | $1.25 | unit | Labor |  | 0 |  |  | Assembly
 | Assemble, 10 kg, Loose | $0.62 | unit | Labor |  | 0 |  |  | Assembly
 | Assemble, 15 kg, Interference | $2.81 | unit | Labor |  | 0 |  |  | Assembly
 | Assemble, 15 kg, Line-on-Line | $1.88 | unit | Labor |  | 0 |  |  | Assembly
 | Assemble, 15 kg, Loose | $0.94 | unit | Labor |  | 0 |  |  | Assembly
 | Assemble, 20 kg, Interference | $3.75 | unit | Labor |  | 0 |  |  | Assembly
 | Assemble, 20 kg, Line-on-Line | $2.50 | unit | Labor |  | 0 |  |  | Assembly
 | Assemble, 20 kg, Loose | $1.25 | unit | Labor |  | 0 |  |  | Assembly
 | Assemble, 3 kg, Interference | $0.56 | unit | Labor |  | 0 |  |  | Assembly
 | Assemble, 3 kg, Line-on-Line | $0.38 | unit | Labor |  | 0 |  |  | Assembly
 | Assemble, 3 kg, Loose | $0.19 | unit | Labor |  | 0 |  |  | Assembly
 | Assemble, 5 kg, Interference | $0.94 | unit | Labor |  | 0 |  |  | Assembly
 | Assemble, 5 kg, Line-on-Line | $0.62 | unit | Labor |  | 0 |  |  | Assembly
 | Assemble, 5 kg, Loose | $0.31 | unit | Labor |  | 0 |  |  | Assembly
 | Brake Bleed - Per Bleeder Valve | $2.50 | unit | Labor |  | 0
 | Brush Apply | $0.02 | cm^2 | Labor |  | 0 |  |  |  |  | For use with glue, adhesives, paint, resin, etc.
 | Cut (scissors, knife) | $0.06 | cm | Labor |  | 0
 | Engine first start, includes fuel | $50.00 | unit | Labor |  | 0 |  |  |  | 40991 | Includes Fuel
 | Heat Treatment | $0.00 | unit | Labor |  | 0 |  |  |  | 2009-04-30 | It is not necessary to include any cost for heat treatment. Included for reference only.
 | Liquid Applicator Gun | $0.02 | cm | Labor |  | 0 |  |  |  |  | For use with glue, adhesives, paint, resin, etc.
 | Liquid Apply - Pour Expanding Foam | $2.00 | m^3 | Labor |  | 0 |  |  |  |  | Cost based on volume of fully expanded final part before trimming
 | Liquid Apply - Spot | $0.10 | unit | Labor |  | 0 |  |  |  |  | For use with glue, adhesives, paint, resin, etc.
 | Machining Setup, Change | $0.65 | unit | Labor |  | 0 |  |  |  | 2009-03-01 | The quantity for this process may be used to scale the cost to the number of parts yielded from each setup. For example if 4 parts can be machined from a single plate then the quantity per part may be set to 0.25 to spread the cost out over each part.
 | Machining Setup, Install and remove | $1.30 | unit | Labor |  | 0 |  |  |  | 2009-03-01 | The quantity for this process may be used to scale the cost to the number of parts yielded from each setup. For example if 4 parts can be machined from a single plate then the quantity per part may be 0.25 to spread the cost out over each part.
 | Riveting | $0.25 | unit | Labor |  | 0 |  |  |  | 2009-02-17
 | Safety Wire, Install | $0.60 | unit | Labor |  | 0 |  |  |  | 2009-02-17 | Unit includes each item or hole included in safety wire path. One item could include bolt, nut, hole in an axle, hub, etc.
 | Suspension Setup - Solid Axle (per corner) | $4.50 | unit | Labor |  | 0
 | Suspension Setup-Independent Susp. (per corner) | $8.75 | unit | Labor |  | 0
 | Tape | $0.80 | m | Labor |  | 0
 | Broach, External | $0.50 | cm | Material Removal |  | 0 |  |  |  | 2009-02-17 | Linear distance of broach
 | Broach, Internal | $0.50 | cm | Material Removal |  | 0 |  |  |  | 2009-02-17 | Linear distance of broach
 | Drilled hole < 50.8 mm dia. | $0.70 | hole | Material Removal |  | 0 |  |  | Drill & Tap |  | Holes >= 50.8 mm must be machined
 | Drilled holes < 25.4 mm dia. | $0.35 | hole | Material Removal |  | 0 |  |  | Drill & Tap
 | EDM - Plunge | $0.30 | cm^3 | Material Removal |  | 0 |  |  | Machining
 | EDM - Wire | $0.20 | cm | Material Removal |  | 0 |  |  | Machining
 | Gear Shaping (hobbing) | $0.50 | cm | Material Removal |  | 0 |  |  | Machining | 2010-05-09 | Linear travel of gear shaping. A half-shaft end 5cm long would cost $2.50
 | Grind, Cylindrical | $0.15 | cm^2 | Material Removal |  | 0 |  |  | Machining |  | 0.25mm machine stock
 | Grind, Flat | $0.15 | cm^2 | Material Removal |  | 0 |  |  | Machining |  | 0.25mm machine stock
 | Grind, Profile | $0.15 | cm^2 | Material Removal |  | 0 |  |  | Machining |  | 0.25mm machine stock
 | Hand Finish - Material Removal | $0.20 | cm^3 | Material Removal |  | 0 |  |  | Machining | 2009-02-20 | Hand sanding, grinding, shaping. Any manual material removal process.
 | Hand Finish - Surface Preperation | $0.02 | cm^2 | Material Removal |  | 0 |  |  | Machining | 2009-02-20 | Hand sanding, cleaning or other operations used to prepare the surface, such as for bonding.
 | Knurling | $0.10 | cm | Material Removal |  | 0 |  |  | Machining | 2009-02-24 | Linear distance of knurl on part (length of knurl, not diameter)
 | Laser Cut | $0.01 | cm | Material Removal |  | 0 |  |  | Machining | 2010-10-24 | Revised cost for 2011 Competition Years
 | Machining | $0.04 | cm^3 | Material Removal |  | 0 |  |  | Machining | 2010-09-25 | Machining can include roughing (1.5mm machine stock min., Tol +/- 0.5mm) and/or finishing (0.5mm machine stock min.). All parts should include the minimum 1.5mm material stock except parts produced by "near net shaped" basic forming processes. It is not necessary to break down rough and finish cuts, only use the correct minimum stock in the calculation of material removed.
 | Mill - Form Cutter | $0.10 | cm | Material Removal |  | 0 |  |  | Machining |  | 0.5mm machine stock min. Linear distance of cutter motion.
 | Non-metallic cutting <= 25.4 mm | $0.35 | cut | Material Removal |  | 0 |  |  | Machining
 | Non-metallic cutting <= 50.8 mm | $0.70 | cut | Material Removal |  | 0 |  |  | Machining
 | Non-metallic cutting <= 76.2 mm | $1.05 | cut | Material Removal |  | 0 |  |  | Machining
 | Non-metallic cutting > 76.2 mm | $1.40 | cut | Material Removal |  | 0 |  |  | Machining
 | Plasma Cutting | $0.10 | cm | Material Removal |  | 0 |  |  | Machining
 | Reemed hole | $0.35 | hole | Material Removal |  | 0 |  |  | Machining |  | Reemed holes must first be drilled or machined
 | Saw or tubing cuts | $0.40 | cm | Material Removal |  | 0 |  |  | Machining
 | Tapping holes | $0.35 | hole | Material Removal |  | 0 |  |  | Drill & Tap
 | Threading, External (machining) | $0.10 | cm | Material Removal |  | 0 |  |  |  | 2009-02-17 | Linear distance of thread (length of bolt thread, not diameter)
 | Threading, Internal (machining) | $0.10 | cm | Material Removal |  | 0 |  |  |  | 2009-02-17 | Linear distance of thread (length of bolt thread, not diameter)
 | Waterjet Cut | $0.01 | cm | Material Removal |  | 0 |  |  | Machining | 2010-10-24 | Revised cost for 2011 Competition Years
 | Spinning, Metal | $0.02 | cm^3 | Shaping |  | 0 |  |  |  | 2009-03-26 | Cost based on the total volume created between the metal starting position and final position.
 | Sheet metal bends | $0.25 | bend | Sheet Materials |  | 0
 | Sheet metal punching | $0.03 | cm^2 | Sheet Materials |  | 0
 | Sheet Metal Saw Cut | $0.20 | cm | Sheet Materials |  | 0 |  |  |  | 2009-02-17 | Includes linear saw cuts and hole saw cuts. Linear cuts by linear distance and hole saw cuts by hole circumference.
 | Sheet metal shearing | $0.25 | cut | Sheet Materials |  | 0
 | Sheet metal stamping | $0.03 | cm^2 | Sheet Materials |  | 0
 | Tube bends | $0.75 | bend | Tubing |  | 0
 | Tube cut | $0.15 | cm | Tubing |  | 0 |  |  |  | 2009-01-24 | Use diameter of tube
 | Tube end preperation for welding | $0.75 | end | Tubing |  | 0 |  |  |  |  | Includes mitering, nothing, sanding, wire wheeling and surface prep. All steps necessary for welding of one tube end except cutting and welding.
 | Tube Flare/Bead | $0.45 | end | Tubing |  | 0 |  |  |  | 2009-02-24 | Form flare or bead for brake lines, cooling lines, etc. in hard lines
 | Weld - Round Tubing | $0.38 | cm | Tubing |  | 0 |  |  |  | 2009-01-24 | Use diameter for dimension. Ratio of pi included.
 |  |  |  |  |  | 70.53758333

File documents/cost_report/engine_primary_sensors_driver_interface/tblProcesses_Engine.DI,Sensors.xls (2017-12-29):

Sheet: Sheet2
Brake Rotor | 10 | 31.41592654 | linear in
 | 0.25 | 4.71238898 | linear in
 |  | 36.12831552 | linear in
 |  | 91.76592141 | linear cm
 |  | 9.176592141

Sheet: Sheet1
Process Table. Posted Version 7, 30-Mar-2012
Process ID | Process | Unit Cost | Unit | Category | numbers | cost | Tooling Required | Near Net Shape | Multiplier Type Used | Modified | Comments
 | Insert Bundle Into Tube or Sleeve | $0.02 | m | Electrical - Bundle Processing | 31.7 | 0.634 |  |  |  | 2009-01-24
 | Shrink Tube | $0.15 | cm | Electrical - Bundle Processing | 1040 | 156 |  |  |  | 2009-03-26
 | Connector Install, Square, Latch/Snap-on Type | $0.17 | unit | Electrical - Connections | 11 | 1.85625
 | Lay Wire - Control | $0.02 | m | Electrical - Layout | 31.7 | 0.634 |  |  |  | 2009-01-25
 | Crimp Wire | $0.17 | unit | Electrical - Prep | 59 | 10.03
 | Cut wire | $0.08 | unit | Electrical - Prep | 59 | 4.916666667
 | Strip Wire | $0.08 | unit | Electrical - Prep | 59 | 4.916666667
 |  |  |  |  |  | 178.9875833

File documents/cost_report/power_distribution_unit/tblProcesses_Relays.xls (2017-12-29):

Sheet: Sheet1
Process Table. Posted Version 7, 30-Mar-2012
Process ID | Process | Unit Cost | Unit | Category | numbers | cost | Tooling Required | Near Net Shape | Multiplier Type Used | Modified | Comments
 | Attach Wire, Wire to screw with nut | $0.65 | unit | Electrical - Attach Wires | 7 | 4.520833333
 | Attach Wire, Wire to terminal block | $0.35 | unit | Electrical - Attach Wires | 3 | 1.0625
 | Shrink Tube | $0.15 | cm | Electrical - Bundle Processing | 25 | 3.75 |  |  |  | 2009-03-26
 | Connector Install, Square, Friction | $0.14 | unit | Electrical - Connections | 4 | 0.5583333333
 | Connector Install, Square, Latch/Snap-on Type | $0.17 | unit | Electrical - Connections | 7 | 1.18125
 | Lay Wire - Power | $0.03 | m | Electrical - Layout | 3 | 0.09 |  |  |  | 2009-01-25
 | Crimp Wire | $0.17 | unit | Electrical - Prep | 12 | 2
 | Cut wire | $0.08 | unit | Electrical - Prep | 12 | 1
 | Strip Wire | $0.08 | unit | Electrical - Prep | 12 | 1
 | Ratchet <= 6.35 mm | $0.50 | unit | Fasteners | 7 | 3.5 |  |  | Fastener Installation
 |  |  |  |  |  | 18.66291667
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

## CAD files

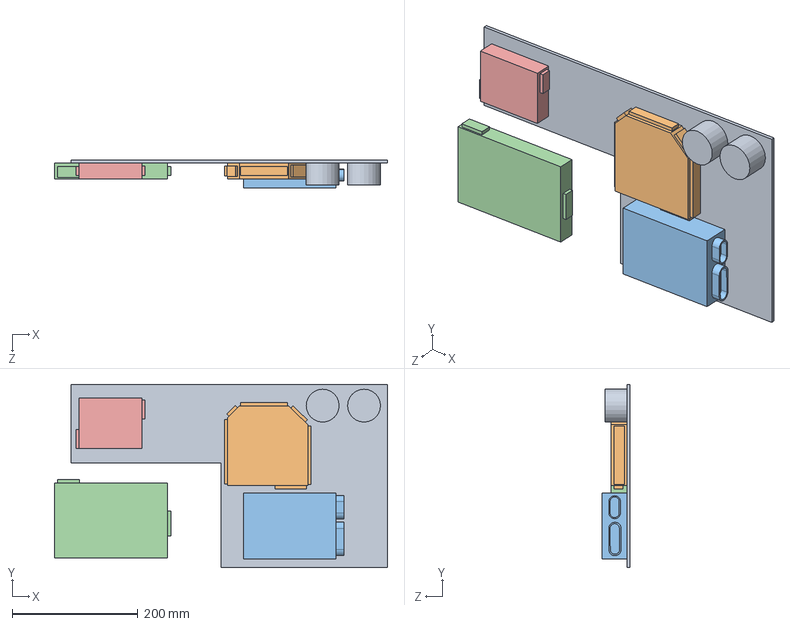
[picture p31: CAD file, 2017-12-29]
documents/solidworks_cad_files/Assem2.SLDASM
530.1 x 292.0 x 45.0 mm
Pannel 1
BMS
Motec
DLS
PMS

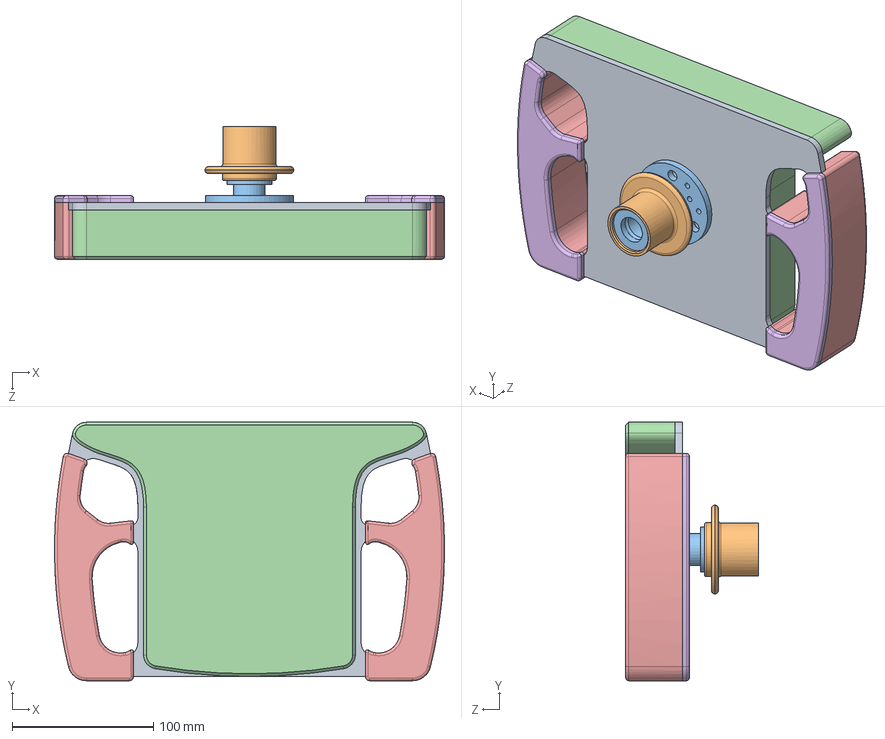
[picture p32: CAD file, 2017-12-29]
documents/solidworks_cad_files/Steering Wheel 2013.SLDASM
276.0 x 183.0 x 93.8 mm
Steering composite plate
QD Inner Flange
QD Outer Flange
Electronic panel
Pads-rr
Pads-fr

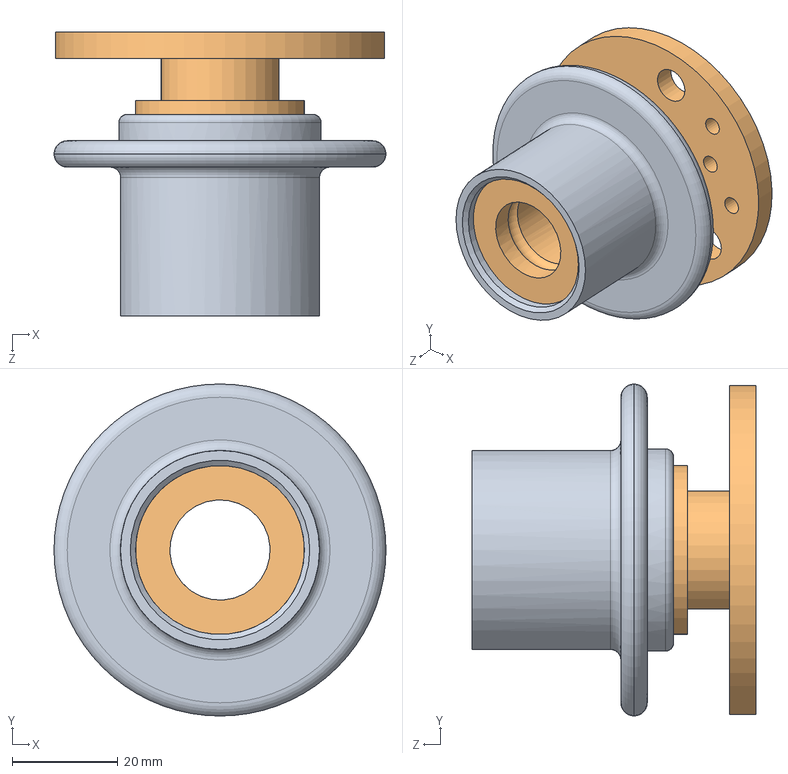
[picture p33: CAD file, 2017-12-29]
documents/solidworks_cad_files/QD assembly.SLDASM
62.9 x 62.9 x 53.8 mm
QD Inner Flange
QD Outer Flange

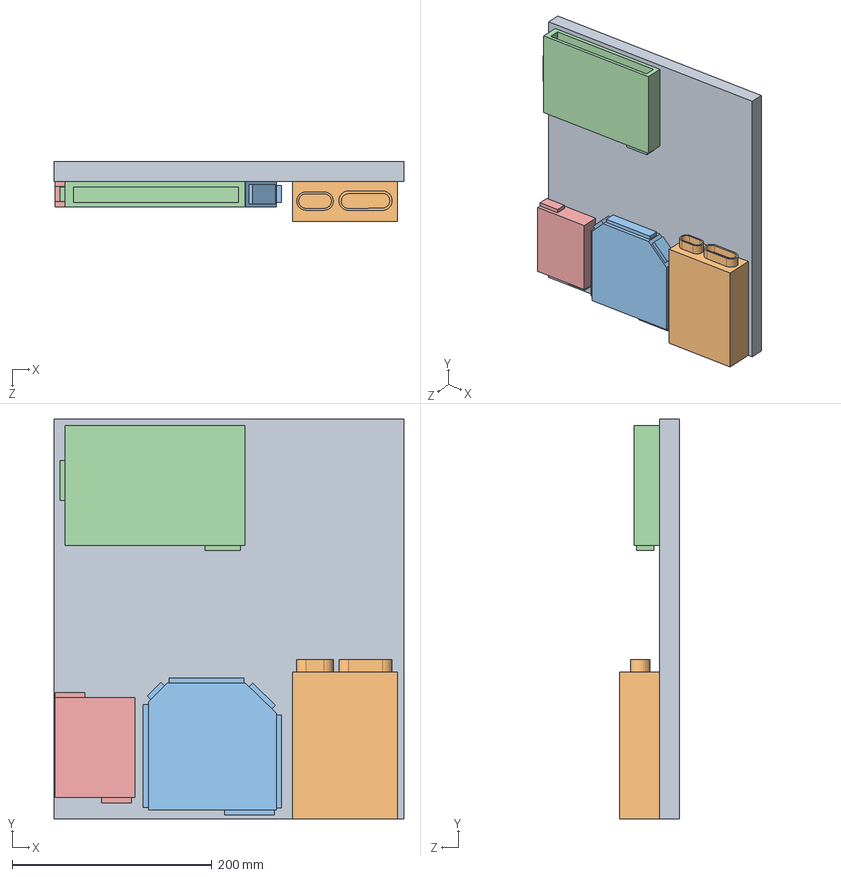
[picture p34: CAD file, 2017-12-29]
documents/solidworks_cad_files/Assem1.SLDASM
350.0 x 400.0 x 60.0 mm
firewall pannel
Motec
BMS
DLS
PMS

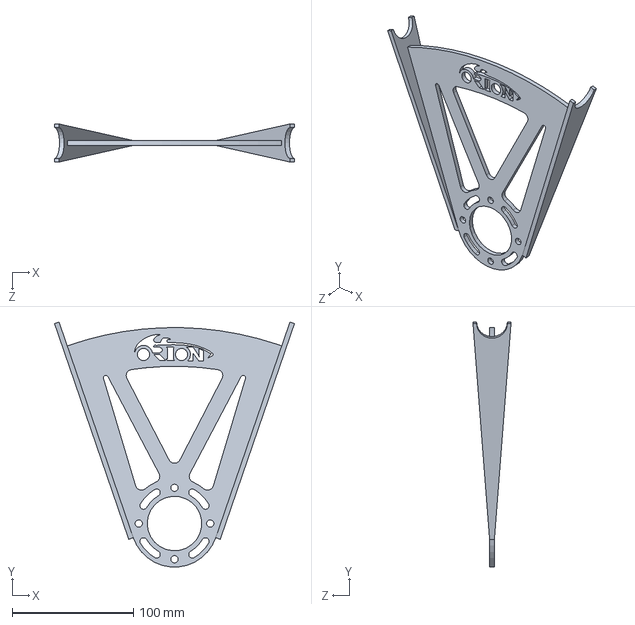
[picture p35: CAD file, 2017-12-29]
documents/solidworks_cad_files/Steering mount 2013.SLDPRT
198.2 x 202.2 x 31.4 mm

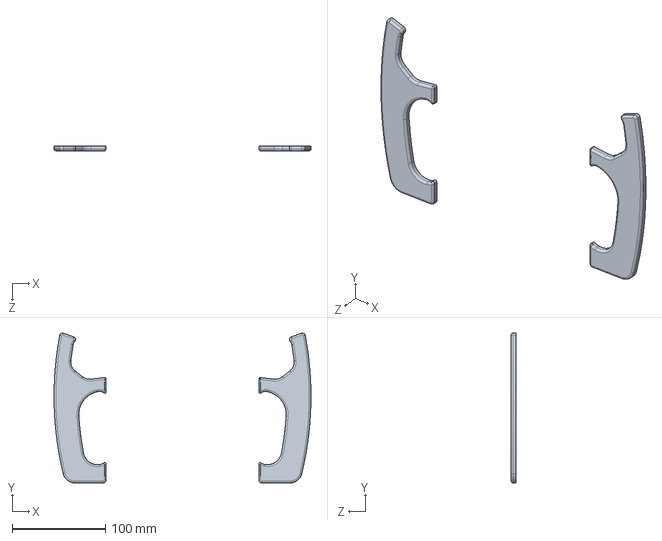
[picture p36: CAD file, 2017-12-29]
documents/solidworks_cad_files/Pads-fr.SLDPRT
276.0 x 161.0 x 5.00 mm

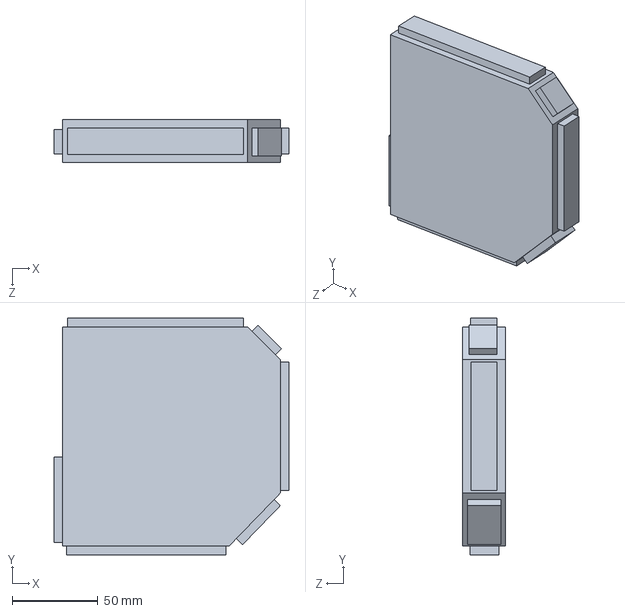
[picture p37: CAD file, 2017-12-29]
documents/solidworks_cad_files/BMS.SLDPRT
137.3 x 138.2 x 25.4 mm

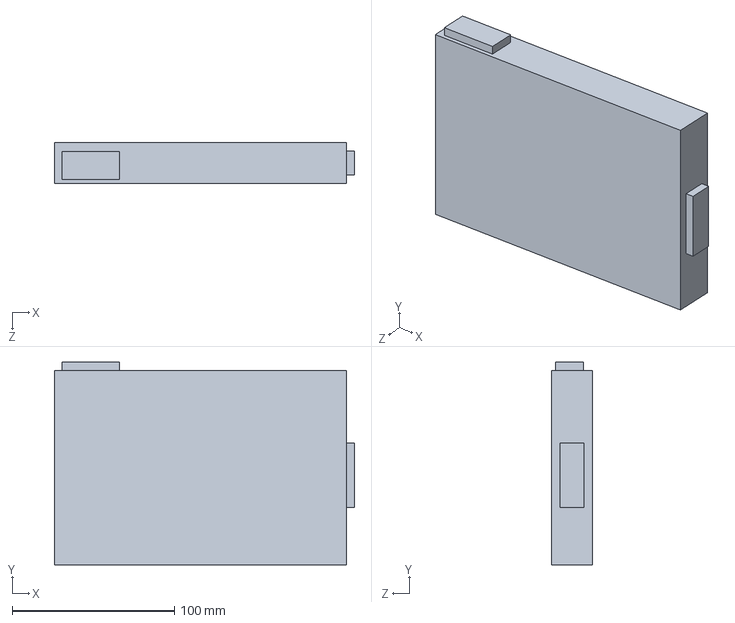
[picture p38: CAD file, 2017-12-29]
documents/solidworks_cad_files/DLS.SLDPRT
185.1 x 125.1 x 25.4 mm

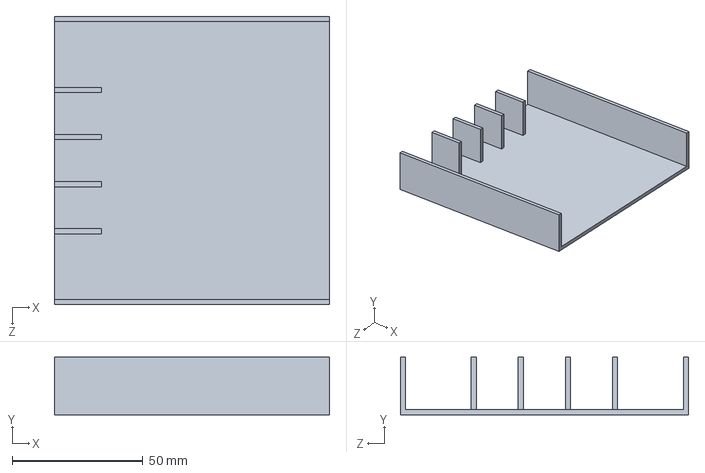
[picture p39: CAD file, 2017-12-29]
documents/solidworks_cad_files/relayboxtop.SLDPRT
105.0 x 22.0 x 110.0 mm

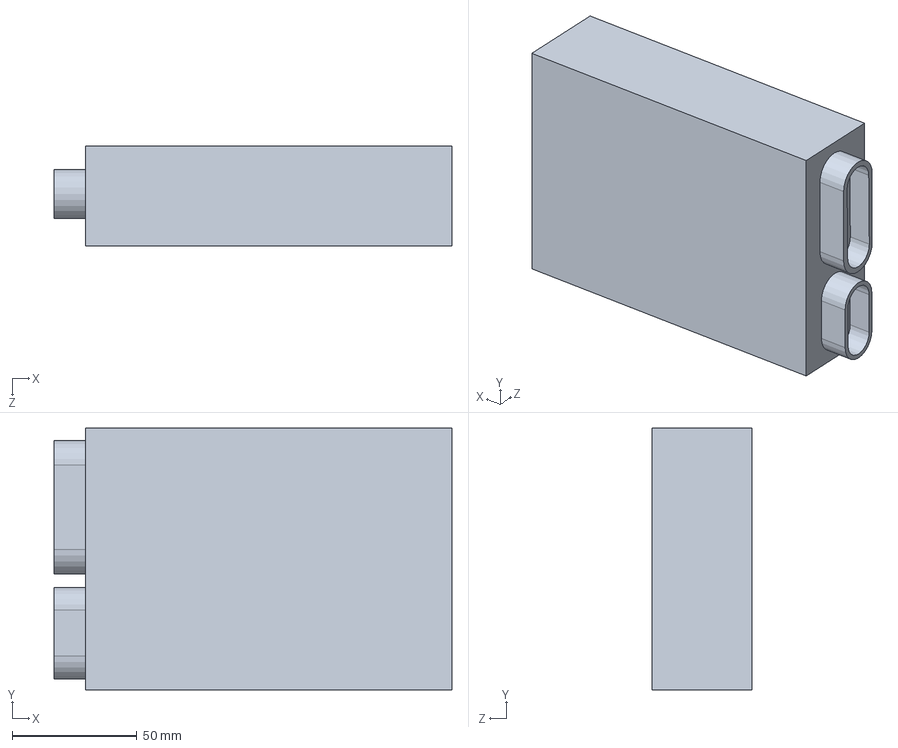
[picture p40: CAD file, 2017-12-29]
documents/solidworks_cad_files/Motec.SLDPRT
159.7 x 105.0 x 40.0 mm

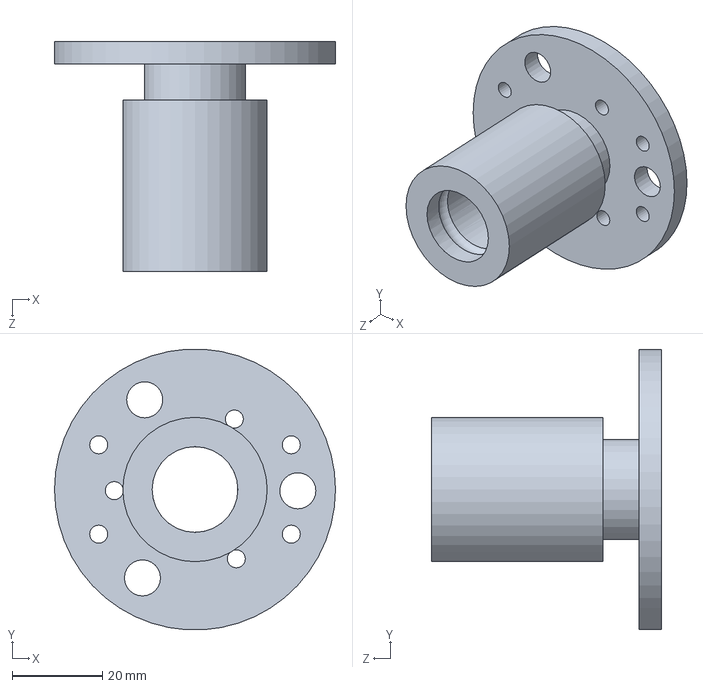
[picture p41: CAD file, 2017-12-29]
documents/solidworks_cad_files/QD Outer Flange.SLDPRT
62.3 x 62.2 x 51.0 mm

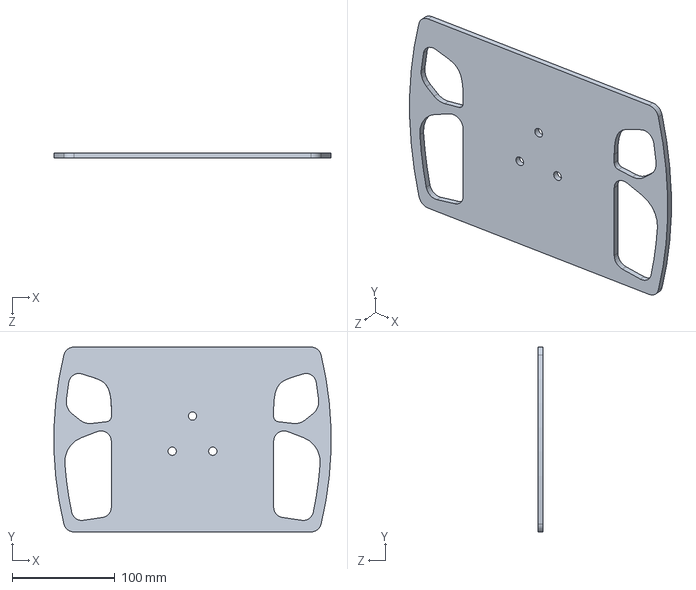
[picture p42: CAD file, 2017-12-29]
documents/solidworks_cad_files/Steering composite plate.SLDPRT
269.6 x 180.0 x 5.00 mm

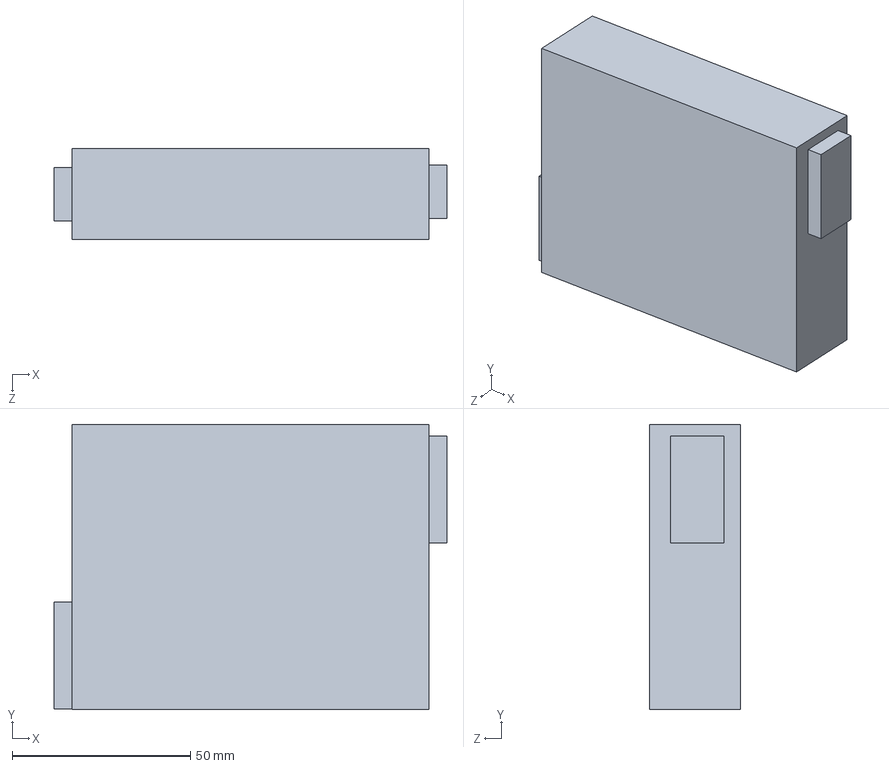
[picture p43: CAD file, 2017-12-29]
documents/solidworks_cad_files/PMS.SLDPRT
110.2 x 80.0 x 25.4 mm

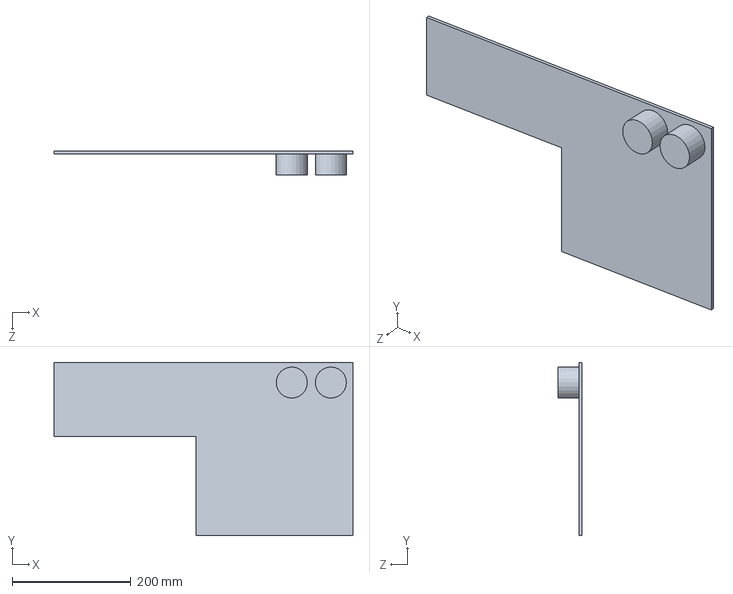
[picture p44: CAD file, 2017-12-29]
documents/solidworks_cad_files/Pannel 1.SLDPRT
504.0 x 292.0 x 40.0 mm

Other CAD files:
documents/solidworks_cad_files/Pipe_3-Assem2.sldasm
documents/solidworks_cad_files/Harness_1-Assem2.sldasm
documents/solidworks_cad_files/Pipe_2-Assem2.sldasm
documents/solidworks_cad_files/Pads-rr.SLDPRT
documents/solidworks_cad_files/Assem2.IGS
documents/solidworks_cad_files/Electronic panel.SLDPRT
documents/solidworks_cad_files/Motec mount.SLDPRT
documents/solidworks_cad_files/QD Inner Flange.SLDPRT
documents/solidworks_cad_files/firewall pannel.SLDPRT
documents/solidworks_cad_files/relayboxbottom.SLDPRT
schematics_images/driver_interface_system/display.skp

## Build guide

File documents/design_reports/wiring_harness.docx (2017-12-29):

CHAPTER 1: ECU AND WIRING

1.1 Introduction and scope:

This report discusses the entire engine and sensor wiring of the car. It includes entire electrical system of the car, their design methodology, selection, wiring loom fabrication and final implementation on the car.

1.2 Goals:

The main and primary goal was to ensure that the wiring does not hamper the performance of the car in any way. Whilst ensuring this, important factors such as wiring weight, cost and volume had to be controlled. Also, the system needed to be designed to ensure easy and quick trouble shooting, especially on field fixing of faults during testing.

1.3 Custom Wiring Harness:

The wiring harness to be used was determined on the ECU to be used. A MoTeC M400 ECU is used on the car and thus a completely custom wiring harness was needed to be designed. The custom harness was designed keeping in mind the specifications of the ECU.

1.4 Electronic casing:

The engine control unit along with the sensor hub and the power distribution module is placed in an enclose box like structure. The decision of shifting the system behind the firewall was taken to provide better ventilation and avoid overheating of the ECU and other electronics components. The temperature of the casing internally during testing was measured to be about 70 degrees under a hot summer sun and the car running for over an hour. The electronics casing made it possible to make sub harnesses as we would have to use connectors to pass wires through the casing wall. This avoided the sub-harnesses to be directly wired. Sub harness greatly simplify replacing faulty/damaged harness without having to make changes to the main harness without adding too much weight. The wiring inside the case interfaced the ECU pins with the connectors located on the surface of the casing. Thus the composite team helped us by manufacturing a glass fibre casing. This was made of fibre-glass so as to avoid any possibility of the casing conducting if it was made of carbon fibre.

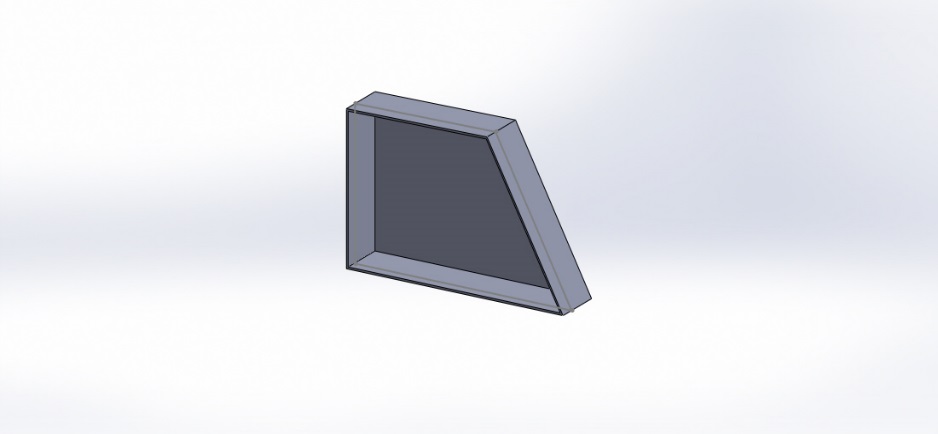
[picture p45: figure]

Figure: 1.1: Electronic Casing

The position of the electronic casing was very carefully decided keeping the factors in mind such as ease of access, keeping the entire casing near the shoulder level of the driver also gives easy access to all of the electronics from the car again and again. Also the casing is placed such that the wire lengths are kept minimum so as to reduce the losses if any, ideally the ECU is to be kept near to the engine. And lowest position possible to keep the centre of gravity as low as possible, thus the casing is placed behind the fire wall in the main roll hoop bracing as shown in the figure.


Figure 1.2: Electronic casing position

1.5 Components inside the casing:

1.5.1 ECU:

We use a MOTEC M400 engine management system as it provides a very advanced, simple and user friendly interface. This helps to make changes to current file or make entirely new file containing the custom fuel map and ignition map which can be easily modified.

M400 is capable of logging data up to 512MB of memory. It can log 64 channels at maximum speed of 200Hz. It also give 8 auxillary outputs, which are used to control the components such as cooling fan and pump, fuel pump and lambda heater. We also use the engine temperature compensation for cold starting.

1.5.2 SENSOR HUB:

A printed circuit board based sensor hub is developed so that the process of interfacing various sensors to the ECU becomes easy. ECU has 8 analog voltage channel inputs, 6 analog temperature inputs and four digital inputs which are used extensively for interfacing sensors such as shock travel sensor, steering angle, throttle position sensor, gear position sensor, fluid pressure sensors and accelerometer on the analog voltage channel; engine temperature and exhaust gas temperature sensors in analog temperature channel and wheel speed sensors in digital channel.

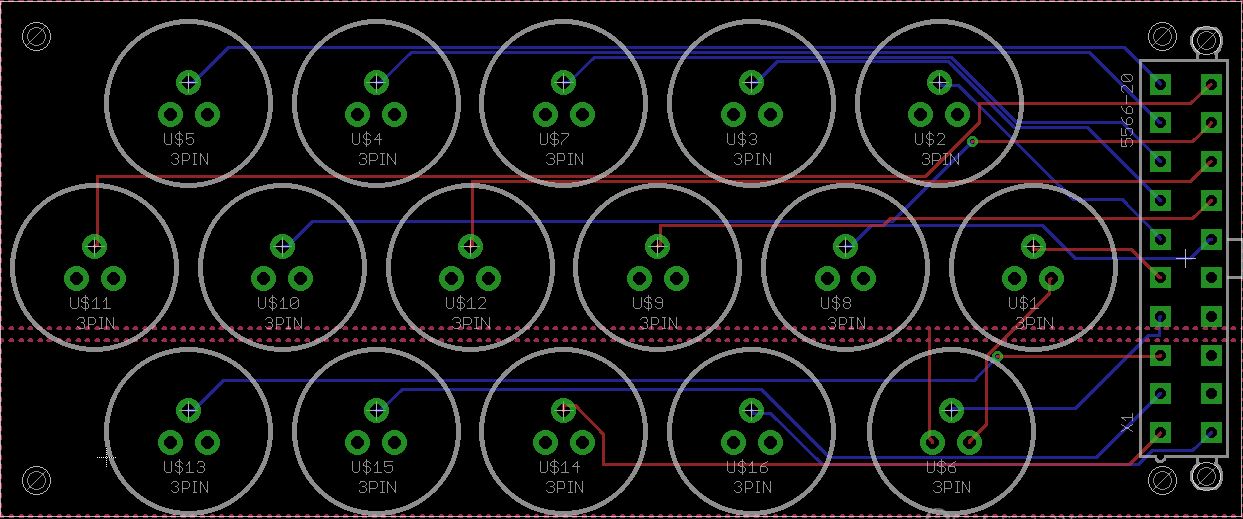
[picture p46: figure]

Figure:1.3: Sensor hub board file

All these sensors can be selectively interfaced with the ECU as and when needed. The sensor hub is made in a panel form so that the connectors can be installed easily and are easy to recognize.

1.6 Connectors:

The connectors which we decided to use on the car were high quality Deutsch connectors which are light weight, sturdy, water proof and also easy to install. We selected the connectors based on various criteria like the number of wires to be carried by the connectors and also the current rating of the connector and the type and size of crimps the connectors accepts.

The Deutsch connectors have a propriety crimping tool and crimps which are sized for different gauges of wires connectors. The crimps get punched from four sides by the crimper, thus ensuring reliable connectivity at all times.

1.7 Wires:

The entire wiring harness was divided into sub harness which can be easily disconnected. These sub harnesses include

- Ignition
- Injector
- Lambda
- Primary Sensors
- Dashboard
- Auxiliary Outputs
- PDM Signals and Outputs
- UTC (CAN-USB)

The selection of wires was done keeping in mind the colour coding and naming to be done. Also the amount of current they will carry is taken into consideration. All the wires are named as well as colour coded. The wiring of the car is divided into three groups – ECU wiring, dash board + wiring and power wiring. The table below shows the wire name, its colour, gauge and the current carrying capacity.

1.7.1 ECU wiring:

NAME /FUNCTION | COLOUR | GAUGE | CURRENT CAPACITY
A1 /AUX-2 | ORANGE | 22 | 5
A2 / 5V ENG | RED | 22 | 5
A3 / IGN-1 | YELLOW | 22 | 5
A4 / IGN-2 | ORANGE | 22 | 5
A5 / IGN-3 | WHITE | 22 | 5
A6 / IGN-4 | PURPLE | 22 | 5
A13 / 8V AUX POWER | RED | 22 | 5
A14 / AV1 | BLUE | 22 | 5
A15 / AV2 | GREEN | 22 | 5
A16 / AV3 | GREEN | 22 | 5
A17 / AV4 | GREEN | 22 | 5
A18 / AUX-1 | WHITE | 22 | 5
A19 / INJ-1 | WHITE-BROWN | 18 | 9
A20 / INJ-2 | WHITE-RED | 18 | 9
A21 / INJ-3 | WHITE-BLUE | 18 | 9
A22 / INJ-4 | WHITE-GREEN | 18 | 9
A23 / AUX-3 | ORANGE | 22 | 5
A24 / AUX-4 | ORANGE | 22 | 5
A25 / AV5 | GREEN | 22 | 5
A26 / 12V | WHITE-RED | 20 | 6
A31 / AUX-5 | ORANGE | 22 | 5
A32 / AUX-6 | ORANGE | 22 | 5
A33 / AUX-7 | ORANGE | 22 | 5
A34 / AUX-8 | ORANGE | 22 | 5
B1 / REF | BLUE | 22 | 5
B2 / SYNC | PURPLE | 22 | 5
B3 / AT1 | GREY | 22 | 5
B4 / AT2 | PURPLE | 22 | 5
B5 / AT3 | YELLOW | 22 | 5
B6 / AT4 | YELLOW | 22 | 5
B7 / AT5 | YELLOW | 22 | 5
B8 / DIG1 | BROWN | 22 | 5
B9 / DIG2 | BROWN | 22 | 5
B10 / DIG3 | BROWN | 22 | 5
B11 / DIG4 | BROWN | 22 | 5
B15 / 0V AUX POWER | BLACK | 22 | 5
B16 / 0V ENGINE | BLACK | 22 | 5
B19 / AT6 | YELLOW | 22 | 5
B20 / AV6 | GREEN | 22 | 5
B21 / AV7 | GREEN | 22 | 5
B22 / AV8 | GREEN | 22 | 5
B23 / CAN HI | WHITE | 22 | 5
B24 / CAN LO | GREEN | 22 | 5
B25 / LA 1S | BLACK | 22 | 5
B26 / LA 1P | RED | 22 | 5
INJECTOR SUPPLY | RED-WHITE | 18 | 9
IGN1-CYL1 | GREEN | 18 | 9
IGN2-CYL2 | WHITE | 18 | 9
IGN4-CYL3 | YELLOW | 18 | 9
IGN3-CYL4 | BROWN | 18 | 9

Table 1.1: ECU wiring

1.7.2 DASH BOARD WIRING:

CONNECTOR PIN NO. | NAME / FUNCTION | FEMALE SIDE COLOUR | MALE SIDE COLOUR | GAUGE | CURRENT CAPACITY (AMP)
1 | FAN ECU | BLUE | BLUE | 22 | 5
2 | FAN | BLUE/BLACK | BLUE | 22 | 5
3 | STARTOR | BLACK | | 22 | 5
4 | IGNITION LED | YELLOW/BLACK | | 22 | 5
5 | CAN HI | WHITE | WHITE | 22 | 5
6 | BRAKE LIGHT SIG | GREEN/BLACK | GREEN | 22 | 5
7 | B16 / 0V ENGINE | YELLOW/BLACK | YELLOW | 22 | 5
13 | PUMP ECU | PURPLE | PURPLE | 22 | 5
14 | PUMP | PURPLE/BLACK | PURPLE | 22 | 5
15 | COCKPIT KILL | ORANGE | ORANGE | 22 | 5
16 | 12 V SUPPLY | RED | RED | 22 | 5
17 | CAN LO | GREEN` | GREEN | 22 | 5
18 | GPS SIGNAL | PINK | ORANGE | 22 | 5
19 | 5 VOLT | RED / BLACK | BLACK | 22 | 5
| BOT | YELLOW | | 22 | 5
| BOT CHASSIS GND | BLACK | | 22 | 5
| BRAKE LIGHT GND | RED | | 22 | 5

Table 1.2: Dashboard wiring

1.7.3 Power wiring:

NAME / FUNCTION | COLOUR | GAUGE | CURRENT CAPACITY
BATTERY POSITIVE | RED | 6 | 37
BATTERY NEGATIVE | BLACK | 6 | 37
FUEL PUMP | BLUE | 16 | 12
COOLING PUMP | BLUE | 18 | 9
COOLING FAN | WHITE BLUE | 18 | 9
STARTOR WIRE | BLACK | 4 | 60

Table 1.3: Power wiring

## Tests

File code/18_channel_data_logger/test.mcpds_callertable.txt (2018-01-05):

main
	ADC1_Init_Advanced
	pll_init
	UART2_Init
		Get_Fosc_kHz
		Delay_100ms
		_Multiply_32x32
		_Modulus_32x32
		_Divide_32x32
	UART1_Init
		Get_Fosc_kHz
		Delay_100ms
		_Multiply_32x32
		_Modulus_32x32
		_Divide_32x32
	UART2_Write
	UART2_Write_Text
		UART2_Write
	ADC1_Get_Sample
	IntToStr
		WordToStr
	UART1_Write
	_Mul_FP
	_Multiply_32x32
	_Sub_FP
		_AddSub_FP
	_AddSub_FP
	_Long2Float
	_Float2Longint

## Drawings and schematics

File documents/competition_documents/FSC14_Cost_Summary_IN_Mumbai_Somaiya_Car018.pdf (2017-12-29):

FSC14 Cost Summary | Car 18 IN Mumbai Somaiya

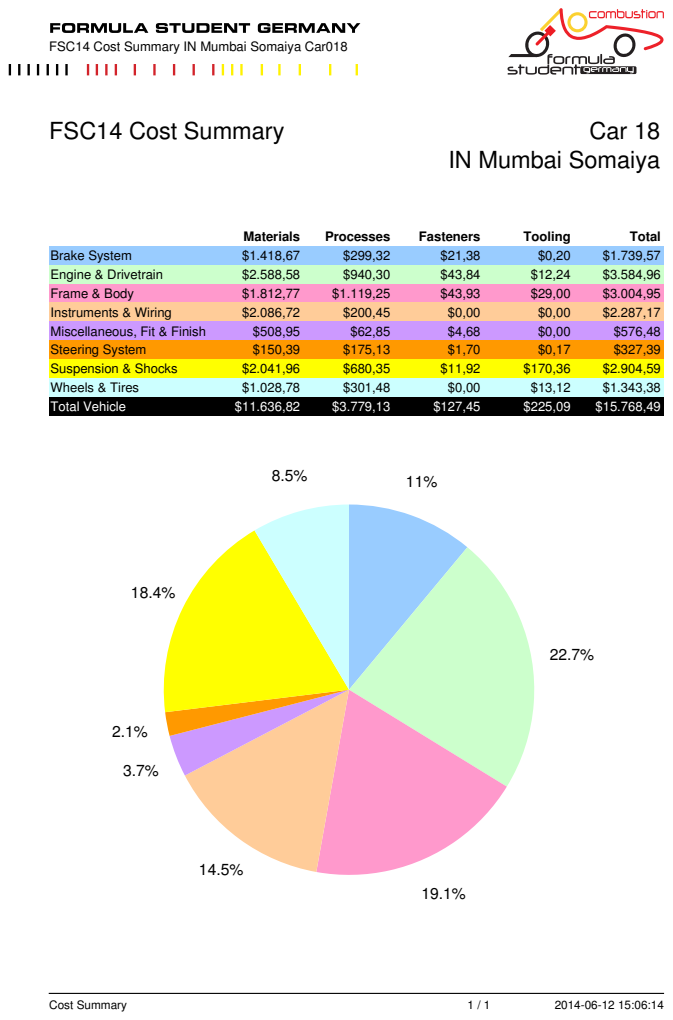
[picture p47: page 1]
Materials; Processes; Fasteners; Tooling; Total; Brake System; Engine & Drivetrain; Frame & Body; Instruments & Wiring; Miscellaneous, Fit & Finish; Steering System; Suspension & Shocks; Wheels & Tires; Total Vehicle; Cost Summary

FSC14 Cost Summary IN Mumbai Somaiya Car018 (http://www.formulastudent.de)

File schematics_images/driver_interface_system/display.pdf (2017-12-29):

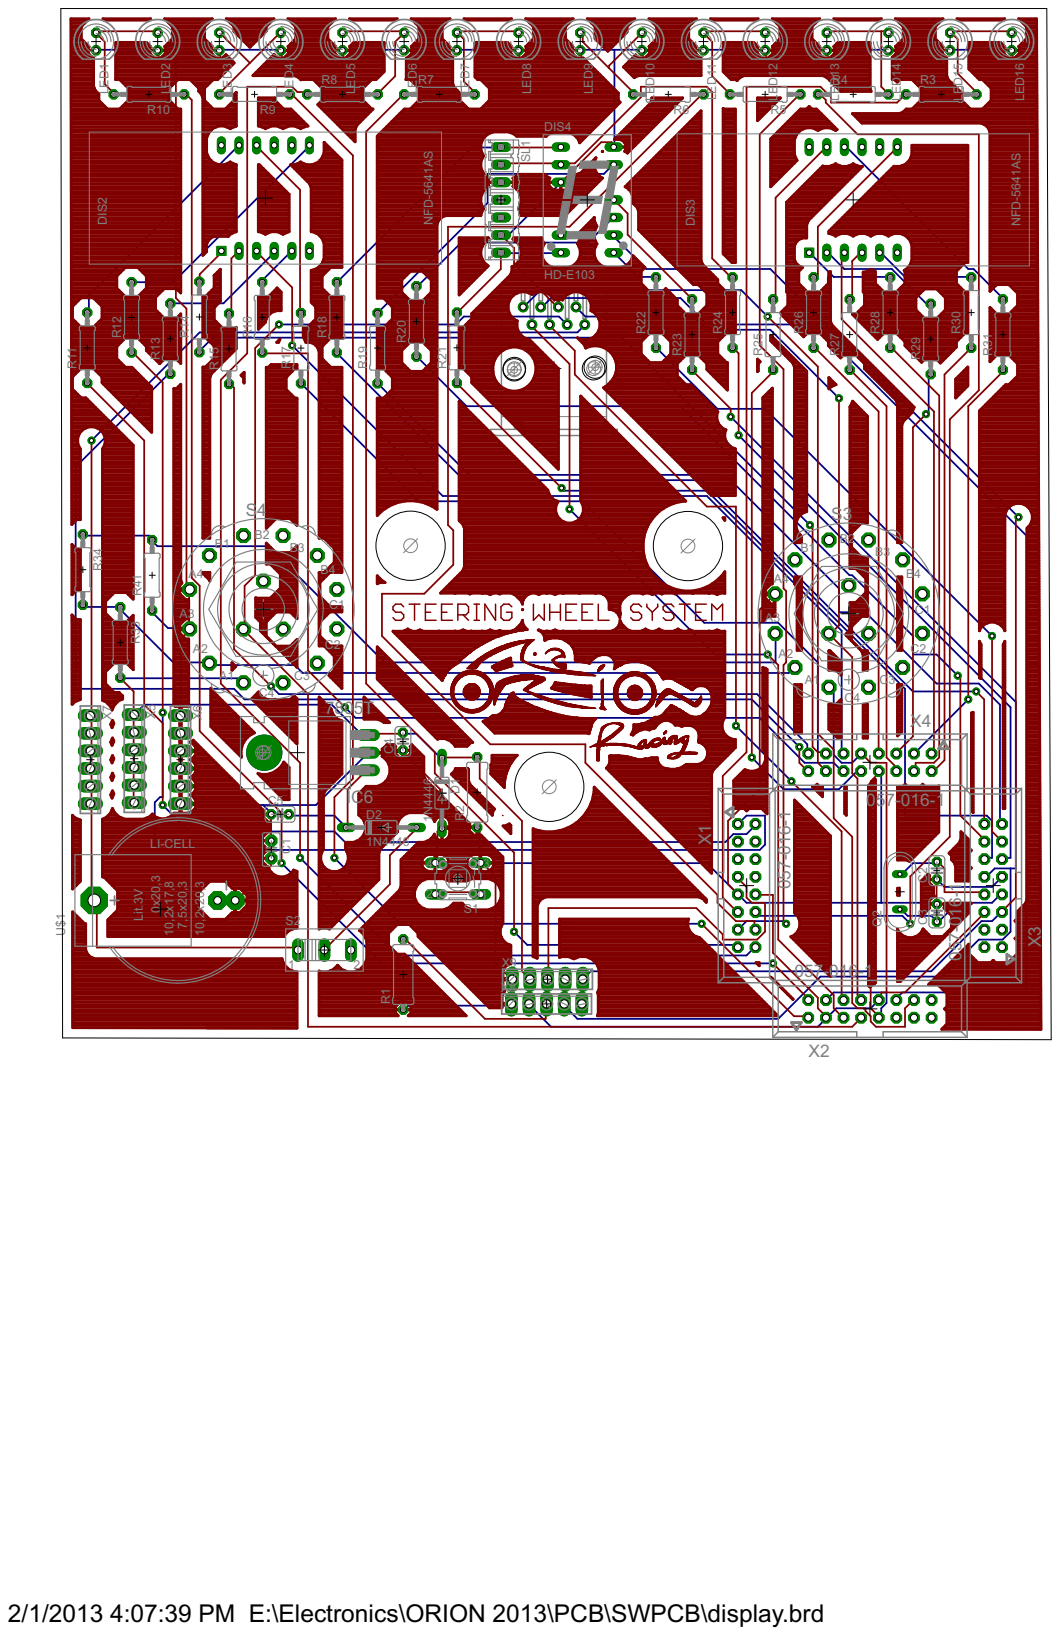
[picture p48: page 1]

2/1/2013 4:07:39 PM E:\Electronics\ORION 2013\PCB\SWPCB\display.brd

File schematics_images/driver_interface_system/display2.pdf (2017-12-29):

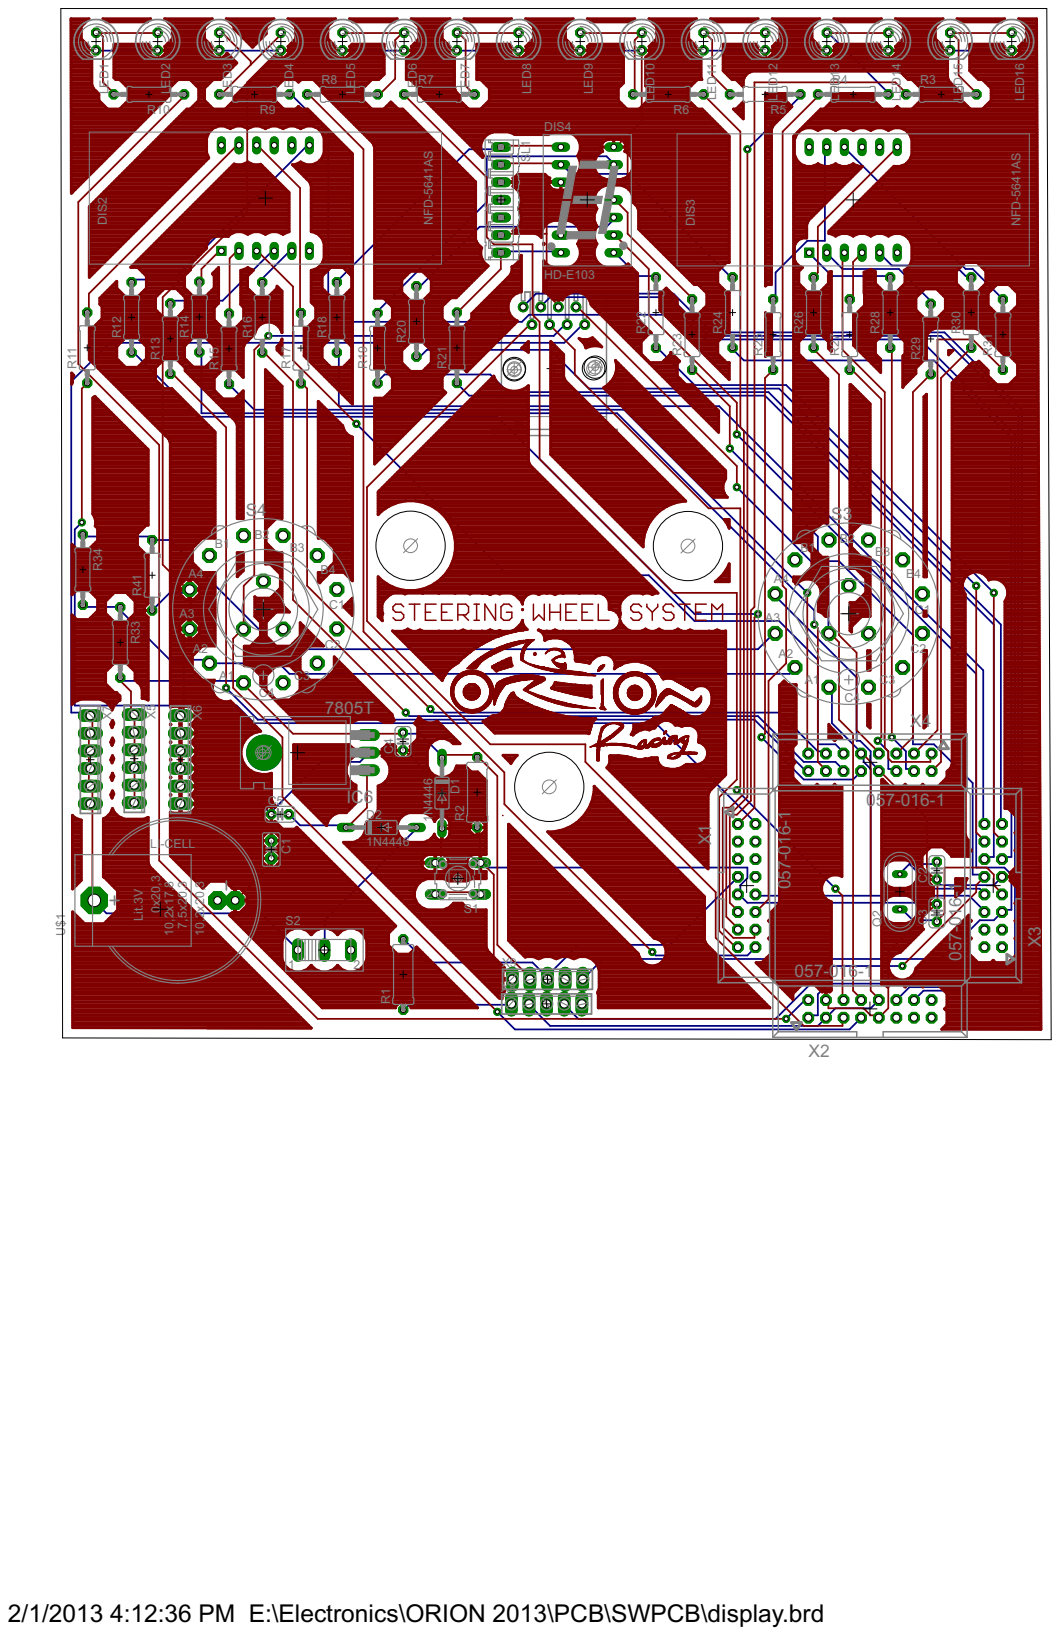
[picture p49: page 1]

2/1/2013 4:12:36 PM E:\Electronics\ORION 2013\PCB\SWPCB\display.brd

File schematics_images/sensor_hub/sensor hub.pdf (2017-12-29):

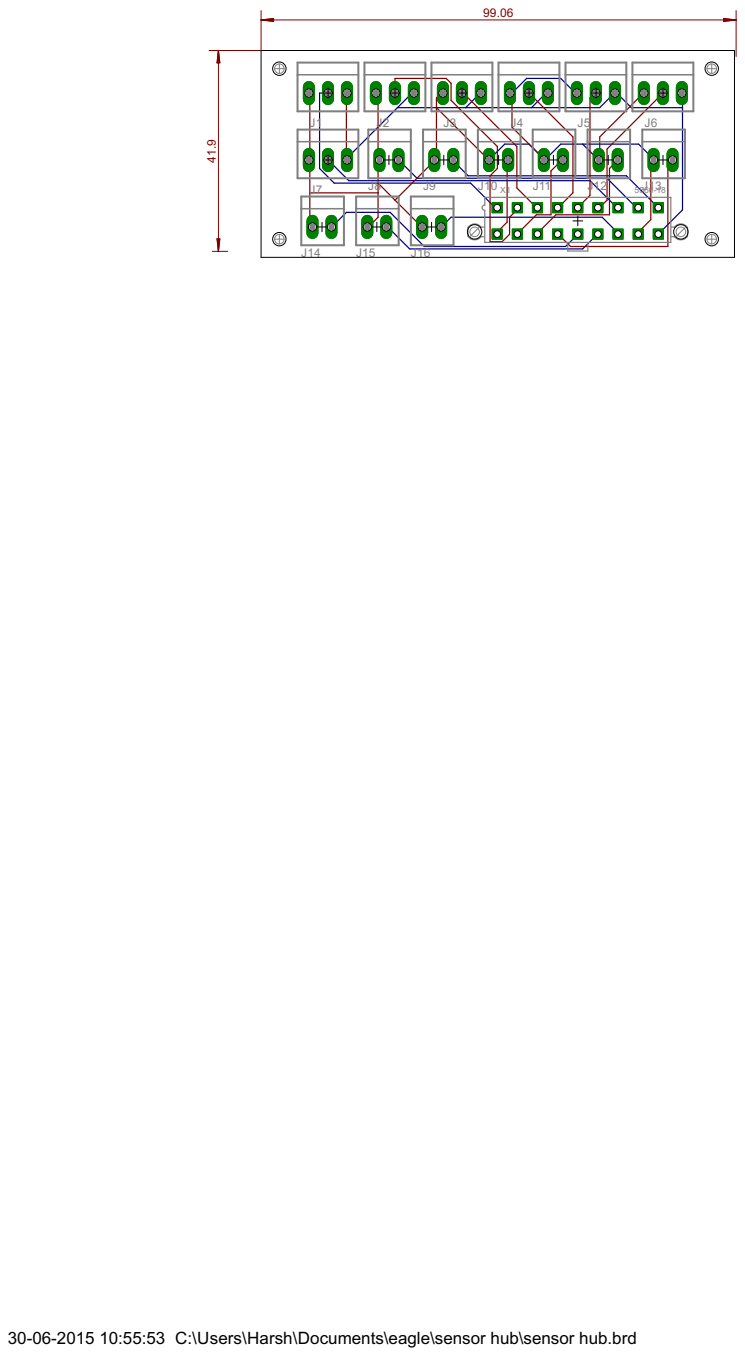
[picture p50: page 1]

30-06-2015 10:55:53 C:\Users\Harsh\Documents\eagle\sensor hub\sensor hub.brd

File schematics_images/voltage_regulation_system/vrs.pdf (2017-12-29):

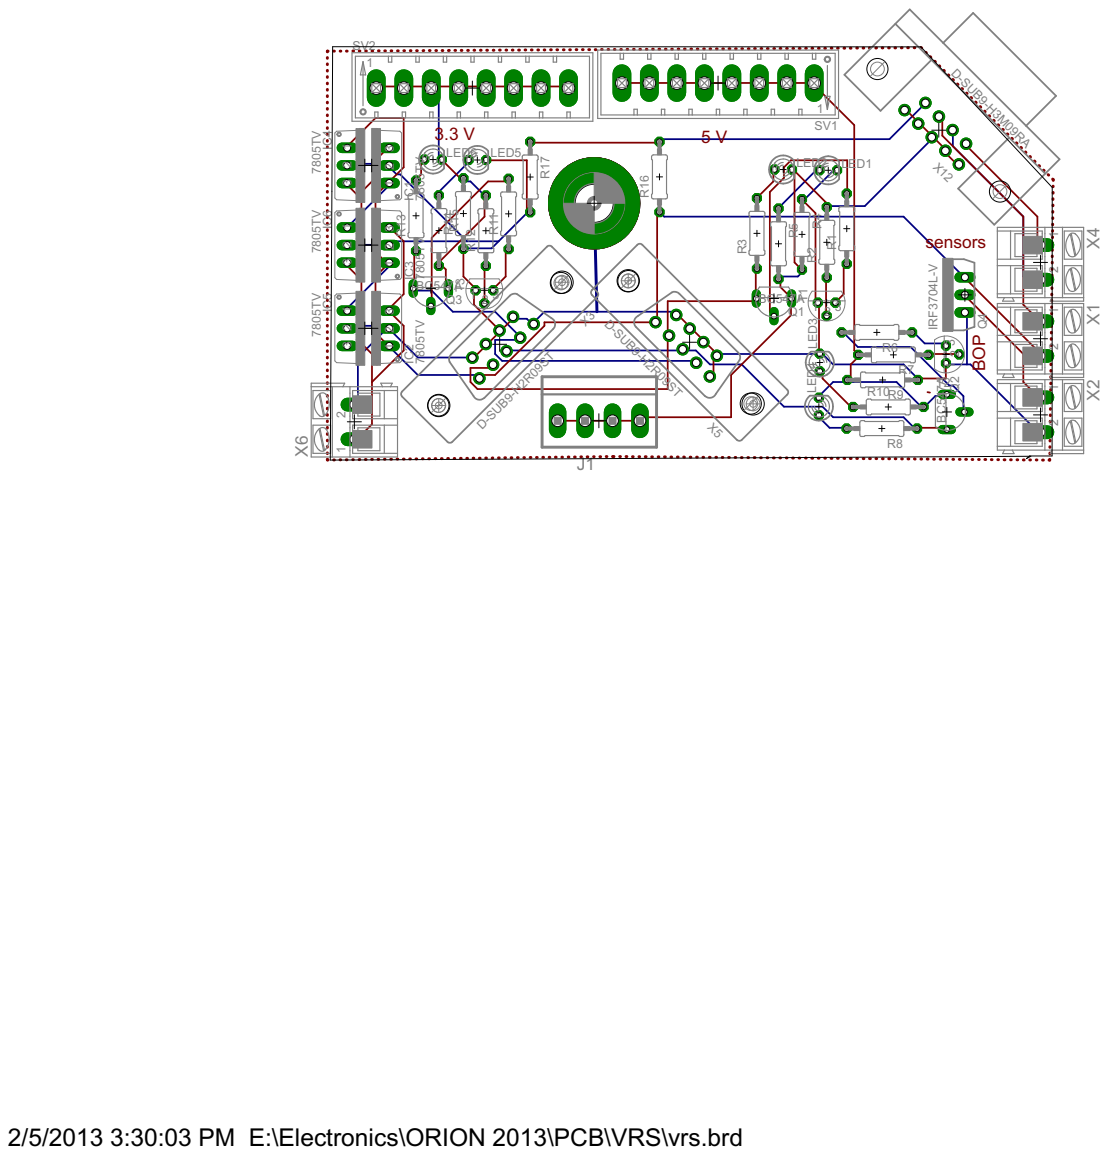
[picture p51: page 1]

2/5/2013 3:30:03 PM E:\Electronics\ORION 2013\PCB\VRS\vrs.brd

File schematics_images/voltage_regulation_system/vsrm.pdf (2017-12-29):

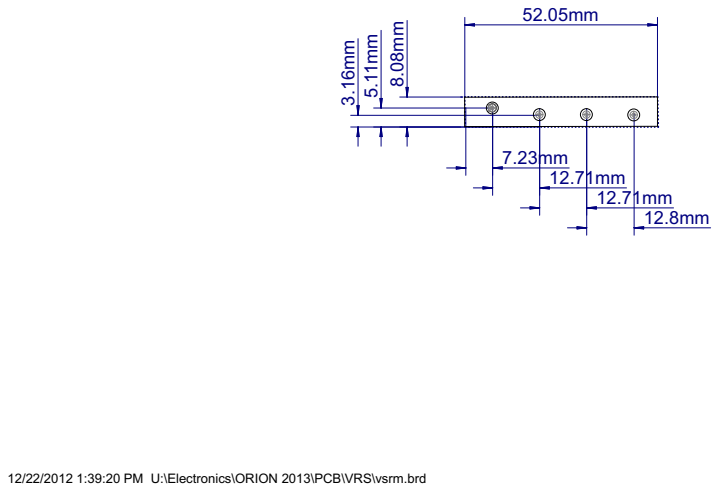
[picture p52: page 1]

12/22/2012 1:39:20 PM U:\Electronics\ORION 2013\PCB\VRS\vsrm.brd

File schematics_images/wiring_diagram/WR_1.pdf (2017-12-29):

# CENTRIFUGAL PUMP COOLING FAN INJTR 1 INJTR 2 INJTR 3 INJTR 4

## BRAKE LIGHT SUPPLY

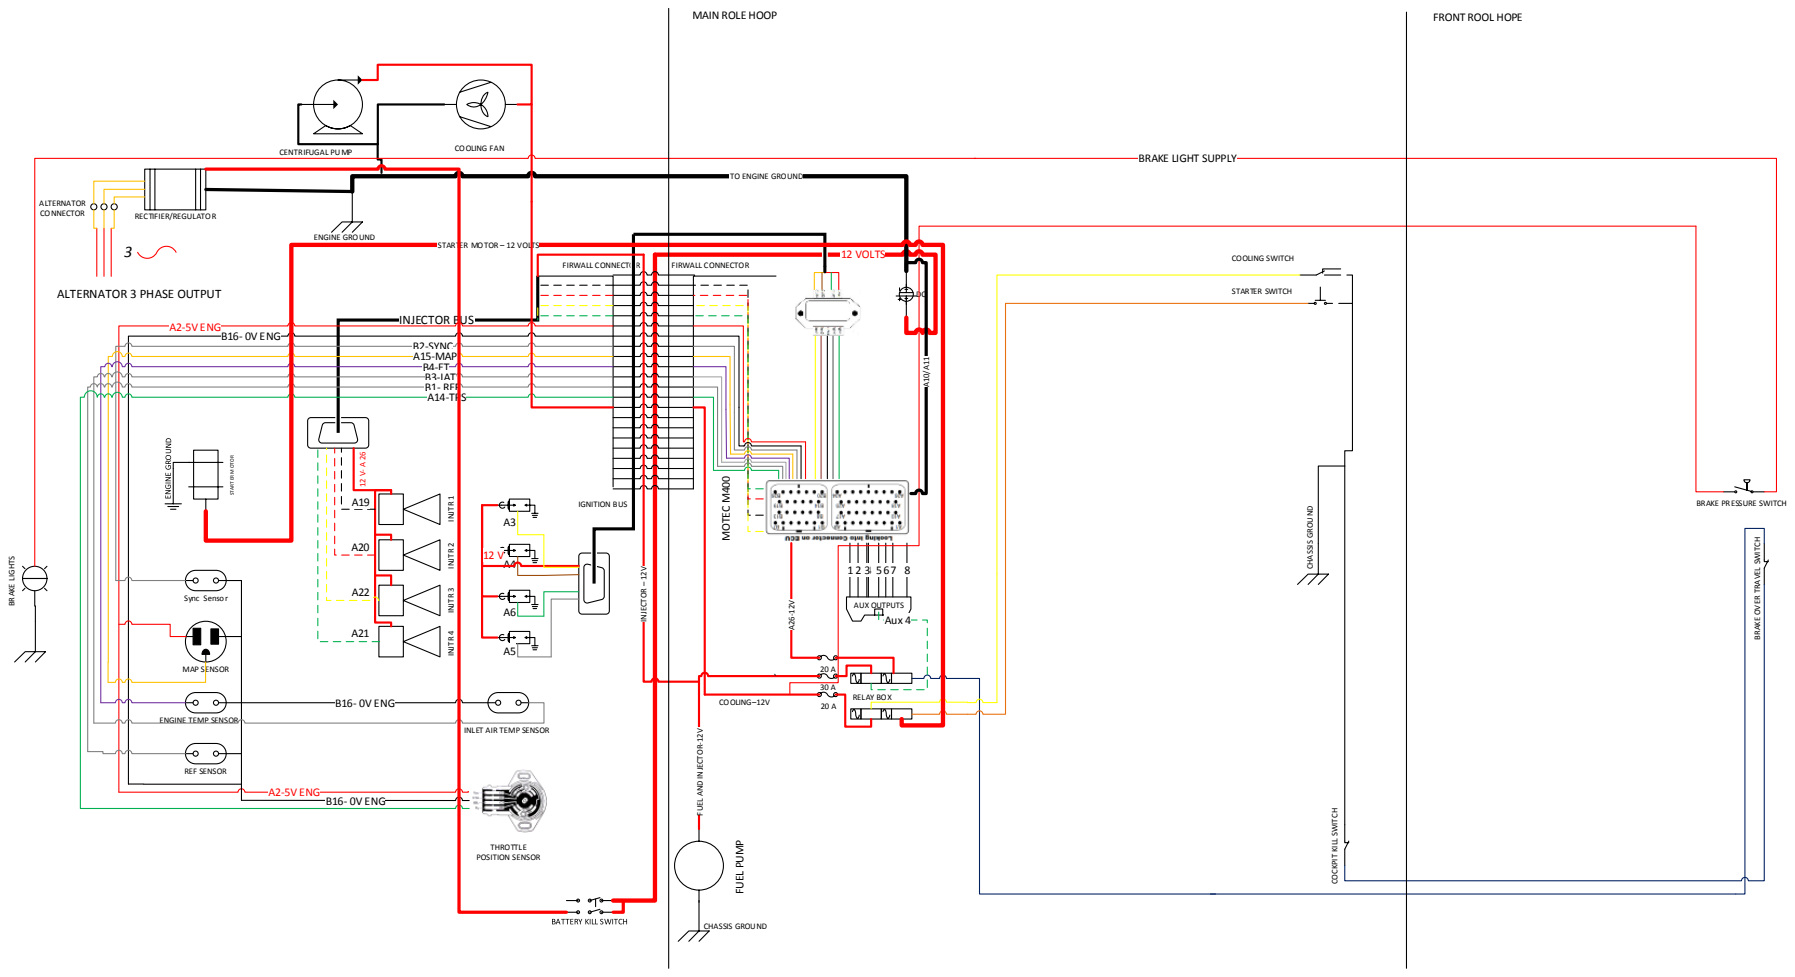
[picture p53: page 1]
12 VOLTS; THROTTLE POSITION SENSOR; REF SENSOR; Sync Sensor; MAP SENSOR; ENGINE GROUND; FIRWALL CONNECTOR; IGNITION BUS; ALTERNATOR CONNECTOR; STARTER M OTO R; RELAY BOX; FUEL PUMP; B16- 0V ENG; A2-5V ENG; B2-SYNC A15-MAP B4-ET B3-IAT B1- REF A14-TPS; INJECTOR – 12V; COOLING–12V; CHASSIS GROUND; AUX OUTPUTS; Aux 4; COOLING SWITCH; STARTER SWITCH; BRAKE LIGHTS; RECTIFIER/REGULATOR

MAIN ROLE HOOP

FRONT ROOL HOPE

TO ENGINE GROUND
FIRWALL CONNECTOR MOTEC M⁴⁰⁰

STARTER MOTOR – 12 VOLTS

ALTERNATOR 3 PHASE OUTPUT

INJECTOR BUS A2-5V ENG

BRAKE PRESSURE SWITCH

BRAKE OVER TRAVEL SWITCH

ENGINE TEMP SENSOR

INLET AIR TEMP SENSOR

FUEL AND INJECTOR-12V

COCKPIT KILL SWITCH

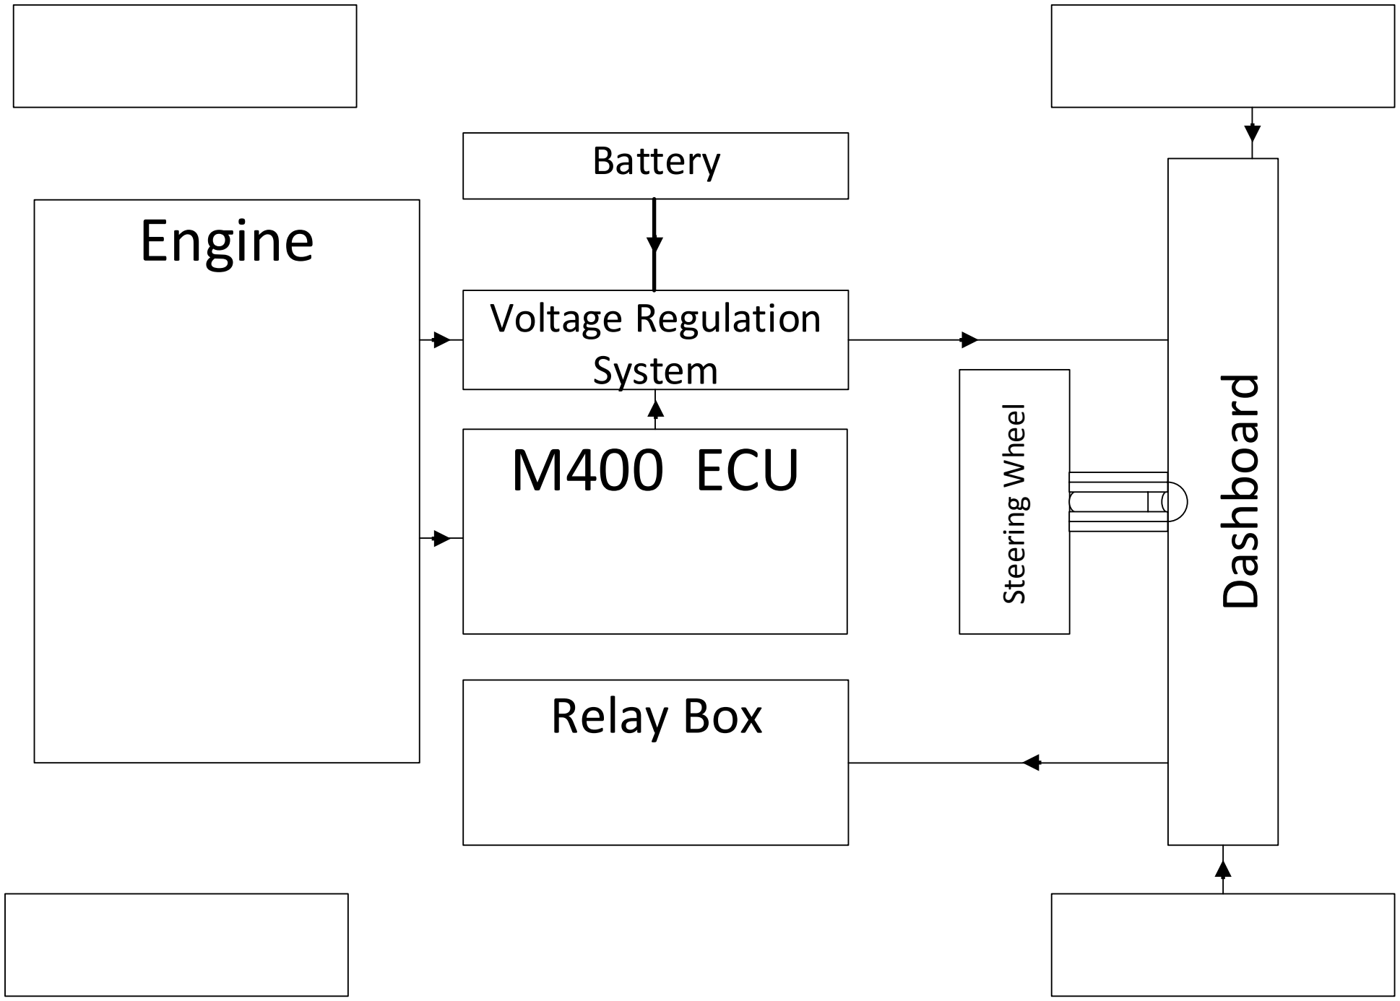
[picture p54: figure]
Steering Wheel; Dashboard; Battery; Voltage Regulation System; Relay Box; Engine; M400 ECU

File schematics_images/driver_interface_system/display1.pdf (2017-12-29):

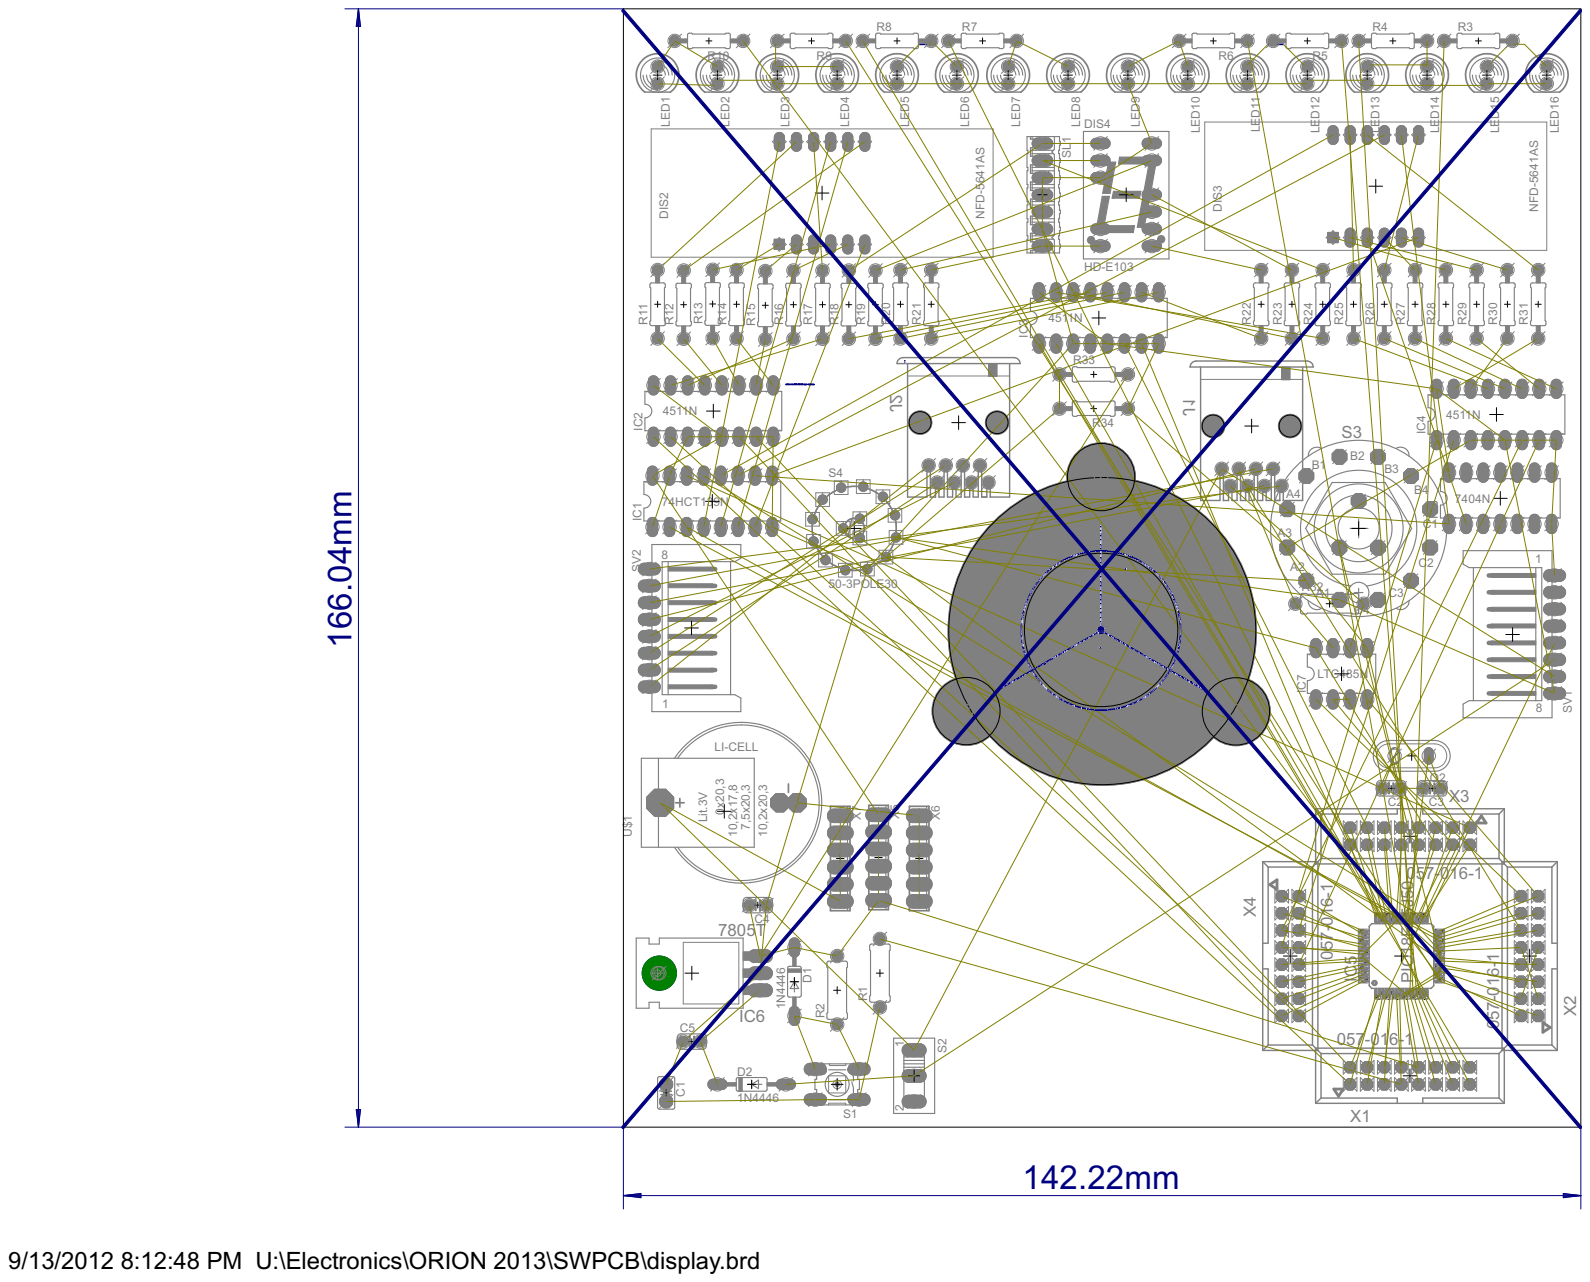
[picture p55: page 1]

9/13/2012 8:12:48 PM U:\Electronics\ORION 2013\SWPCB\display.brd

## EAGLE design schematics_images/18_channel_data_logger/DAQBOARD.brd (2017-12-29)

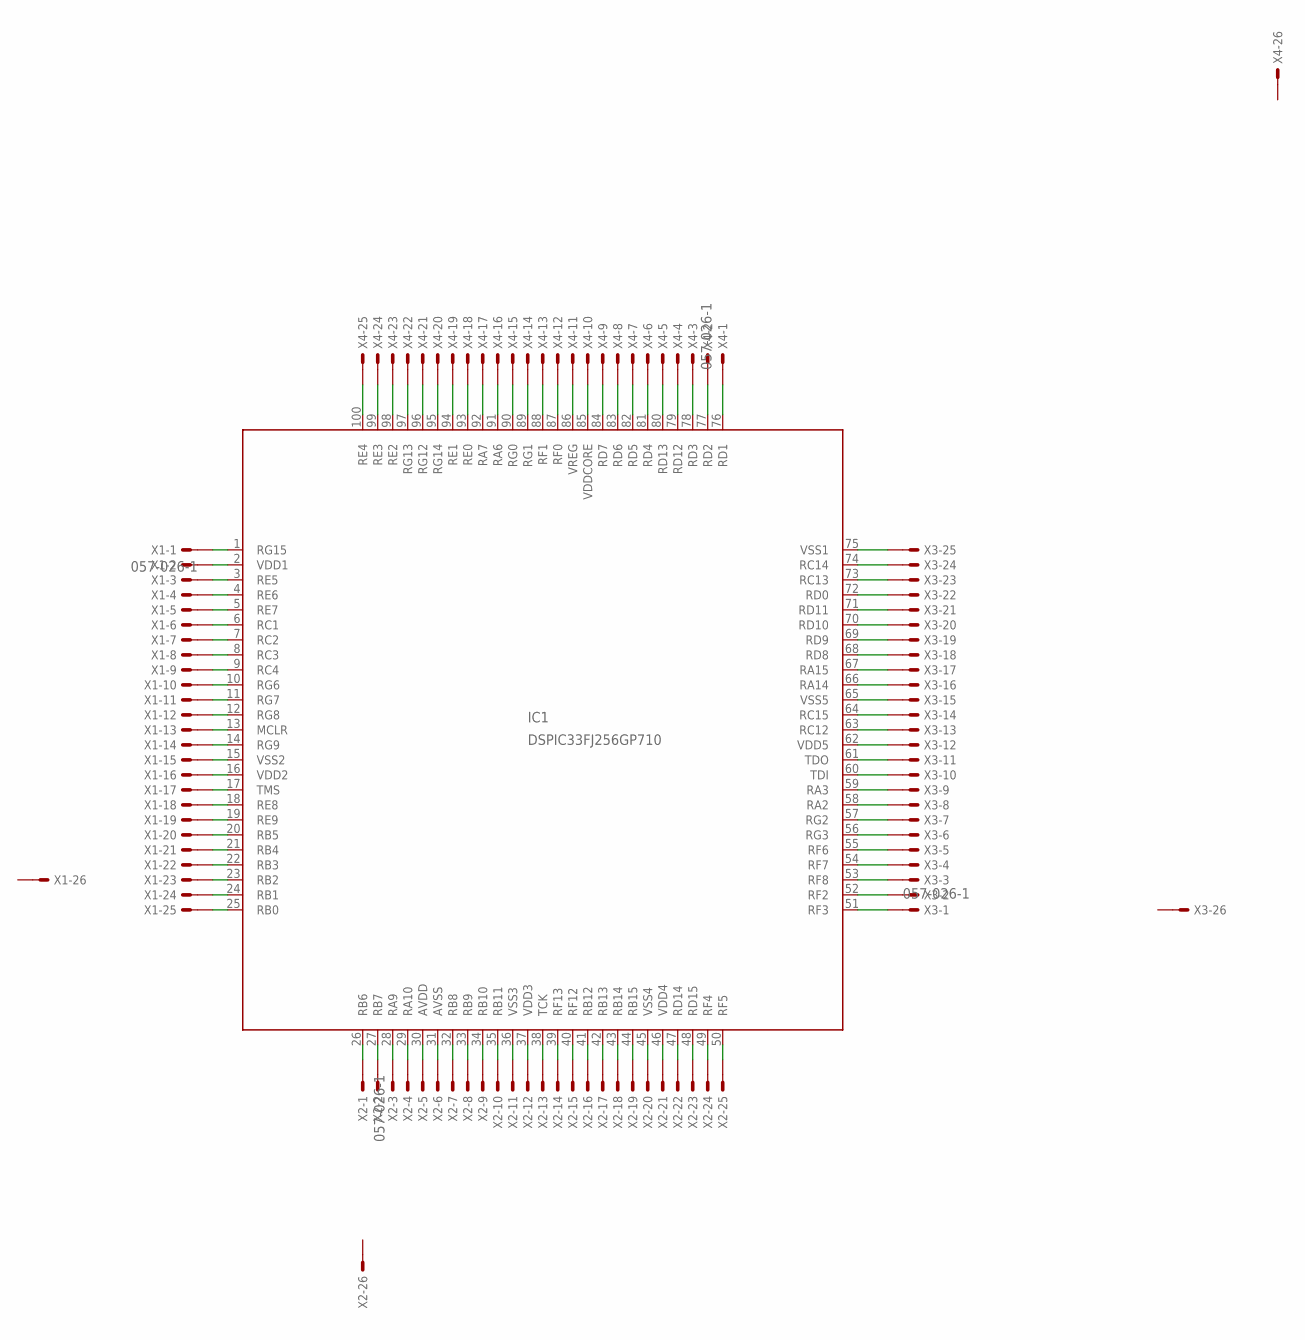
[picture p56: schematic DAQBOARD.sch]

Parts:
IC1: DSPIC33FJ256GP710; TQFP100-12X12
X1, X2, X3, X4: 057-026-1

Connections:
unnamed: IC1.1 (RG15), X1.1
unnamed: IC1.2 (VDD1), X1.2
unnamed: IC1.3 (RE5), X1.3
unnamed: IC1.4 (RE6), X1.4
unnamed: IC1.5 (RE7), X1.5
unnamed: IC1.6 (RC1), X1.6
unnamed: IC1.7 (RC2), X1.7
unnamed: IC1.8 (RC3), X1.8
unnamed: IC1.9 (RC4), X1.9
unnamed: IC1.10 (RG6), X1.10
unnamed: IC1.11 (RG7), X1.11
unnamed: IC1.12 (RG8), X1.12
unnamed: IC1.13 (MCLR), X1.13
unnamed: IC1.14 (RG9), X1.14
unnamed: IC1.15 (VSS2), X1.15
unnamed: IC1.16 (VDD2), X1.16
unnamed: IC1.17 (TMS), X1.17
unnamed: IC1.18 (RE8), X1.18
unnamed: IC1.19 (RE9), X1.19
unnamed: IC1.20 (RB5), X1.20
unnamed: IC1.21 (RB4), X1.21
unnamed: IC1.22 (RB3), X1.22
unnamed: IC1.23 (RB2), X1.23
unnamed: IC1.24 (RB1), X1.24
unnamed: IC1.25 (RB0), X1.25
unnamed: IC1.26 (RB6), X2.1
unnamed: IC1.27 (RB7), X2.2
unnamed: IC1.28 (RA9), X2.3
unnamed: IC1.29 (RA10), X2.4
unnamed: IC1.30 (AVDD), X2.5
unnamed: IC1.31 (AVSS), X2.6
unnamed: IC1.32 (RB8), X2.7
unnamed: IC1.33 (RB9), X2.8
unnamed: IC1.34 (RB10), X2.9
unnamed: IC1.35 (RB11), X2.10
unnamed: IC1.36 (VSS3), X2.11
unnamed: IC1.37 (VDD3), X2.12
unnamed: IC1.38 (TCK), X2.13
unnamed: IC1.39 (RF13), X2.14
unnamed: IC1.40 (RF12), X2.15
unnamed: IC1.41 (RB12), X2.16
unnamed: IC1.42 (RB13), X2.17
unnamed: IC1.43 (RB14), X2.18
unnamed: IC1.44 (RB15), X2.19
unnamed: IC1.45 (VSS4), X2.20
unnamed: IC1.46 (VDD4), X2.21
unnamed: IC1.47 (RD14), X2.22
unnamed: IC1.48 (RD15), X2.23
unnamed: IC1.49 (RF4), X2.24
unnamed: IC1.50 (RF5), X2.25
unnamed: IC1.51 (RF3), X3.1
unnamed: IC1.52 (RF2), X3.2
unnamed: IC1.53 (RF8), X3.3
unnamed: IC1.54 (RF7), X3.4
unnamed: IC1.55 (RF6), X3.5
unnamed: IC1.56 (RG3), X3.6
unnamed: IC1.57 (RG2), X3.7
unnamed: IC1.58 (RA2), X3.8
unnamed: IC1.59 (RA3), X3.9
unnamed: IC1.60 (TDI), X3.10
unnamed: IC1.61 (TDO), X3.11
unnamed: IC1.62 (VDD5), X3.12
unnamed: IC1.63 (RC12), X3.13
unnamed: IC1.64 (RC15), X3.14
unnamed: IC1.65 (VSS5), X3.15
unnamed: IC1.66 (RA14), X3.16
unnamed: IC1.67 (RA15), X3.17
unnamed: IC1.68 (RD8), X3.18
unnamed: IC1.69 (RD9), X3.19
unnamed: IC1.70 (RD10), X3.20
unnamed: IC1.71 (RD11), X3.21
unnamed: IC1.72 (RD0), X3.22
unnamed: IC1.73 (RC13), X3.23
unnamed: IC1.74 (RC14), X3.24
unnamed: IC1.75 (VSS1), X3.25
unnamed: IC1.76 (RD1), X4.1
unnamed: IC1.77 (RD2), X4.2
unnamed: IC1.78 (RD3), X4.3
unnamed: IC1.79 (RD12), X4.4
unnamed: IC1.80 (RD13), X4.5
unnamed: IC1.81 (RD4), X4.6
unnamed: IC1.82 (RD5), X4.7
unnamed: IC1.83 (RD6), X4.8
unnamed: IC1.84 (RD7), X4.9
unnamed: IC1.85 (VDDCORE), X4.10
unnamed: IC1.86 (VREG), X4.11
unnamed: IC1.87 (RF0), X4.12
unnamed: IC1.88 (RF1), X4.13
unnamed: IC1.89 (RG1), X4.14
unnamed: IC1.90 (RG0), X4.15
unnamed: IC1.91 (RA6), X4.16
unnamed: IC1.92 (RA7), X4.17
unnamed: IC1.93 (RE0), X4.18
unnamed: IC1.94 (RE1), X4.19
unnamed: IC1.95 (RG14), X4.20
unnamed: IC1.96 (RG12), X4.21
unnamed: IC1.97 (RG13), X4.22
unnamed: IC1.98 (RE2), X4.23
unnamed: IC1.99 (RE3), X4.24
unnamed: IC1.100 (RE4), X4.25

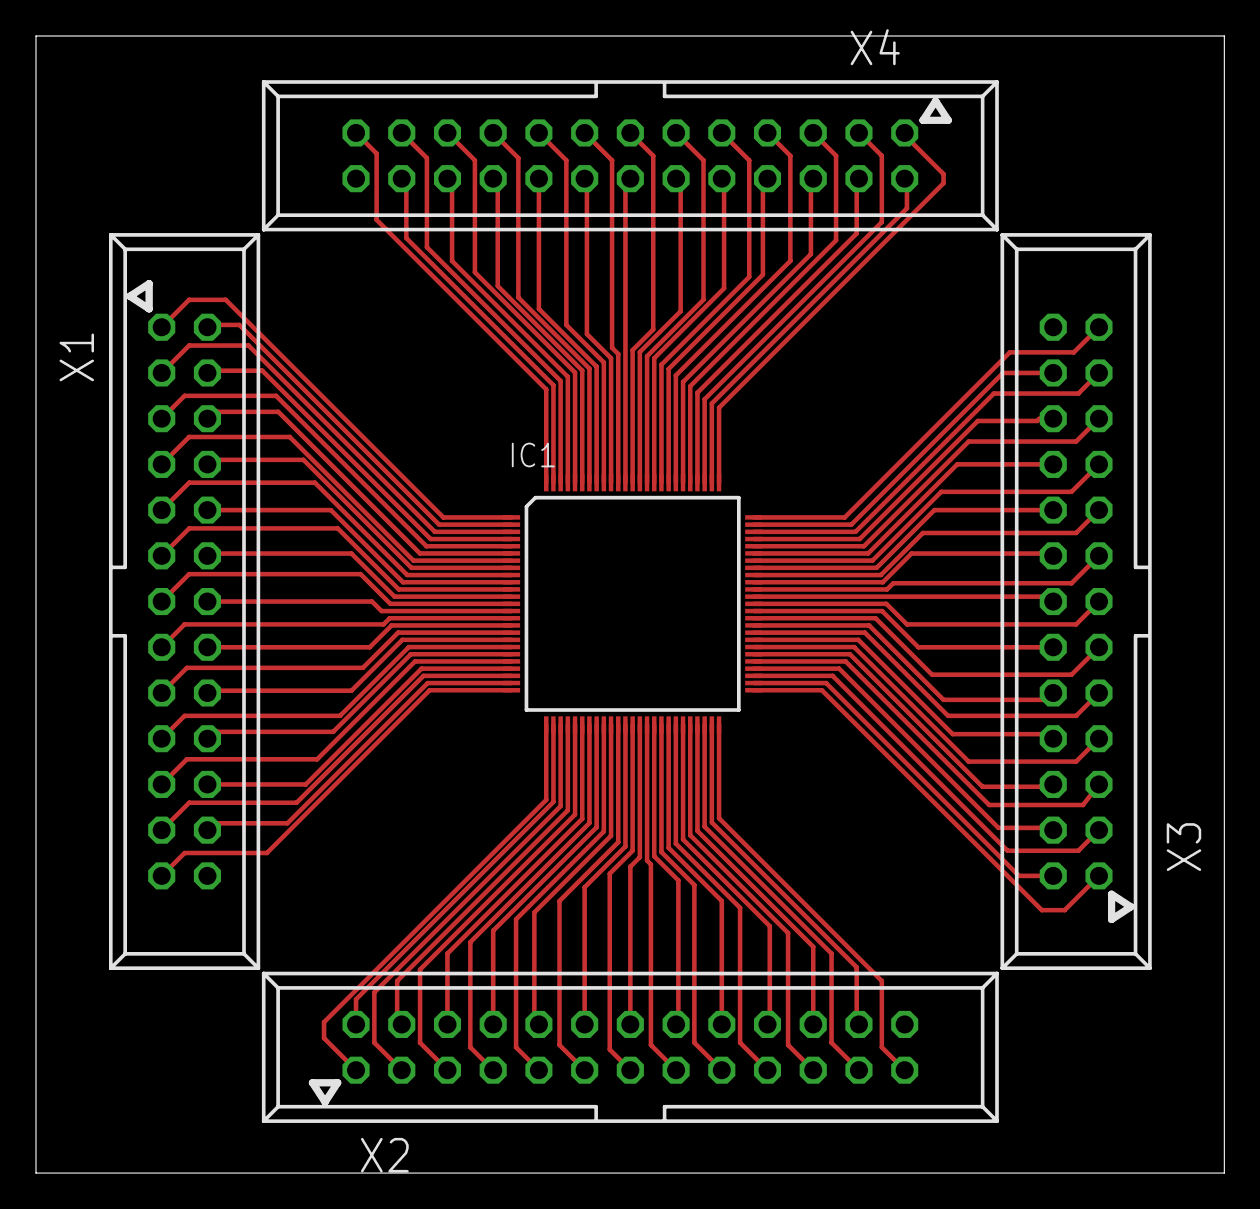
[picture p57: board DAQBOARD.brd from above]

Board: 2 copper layers, 66.0 x 63.2 mm, 5 parts (0 on the bottom side), 100 nets.

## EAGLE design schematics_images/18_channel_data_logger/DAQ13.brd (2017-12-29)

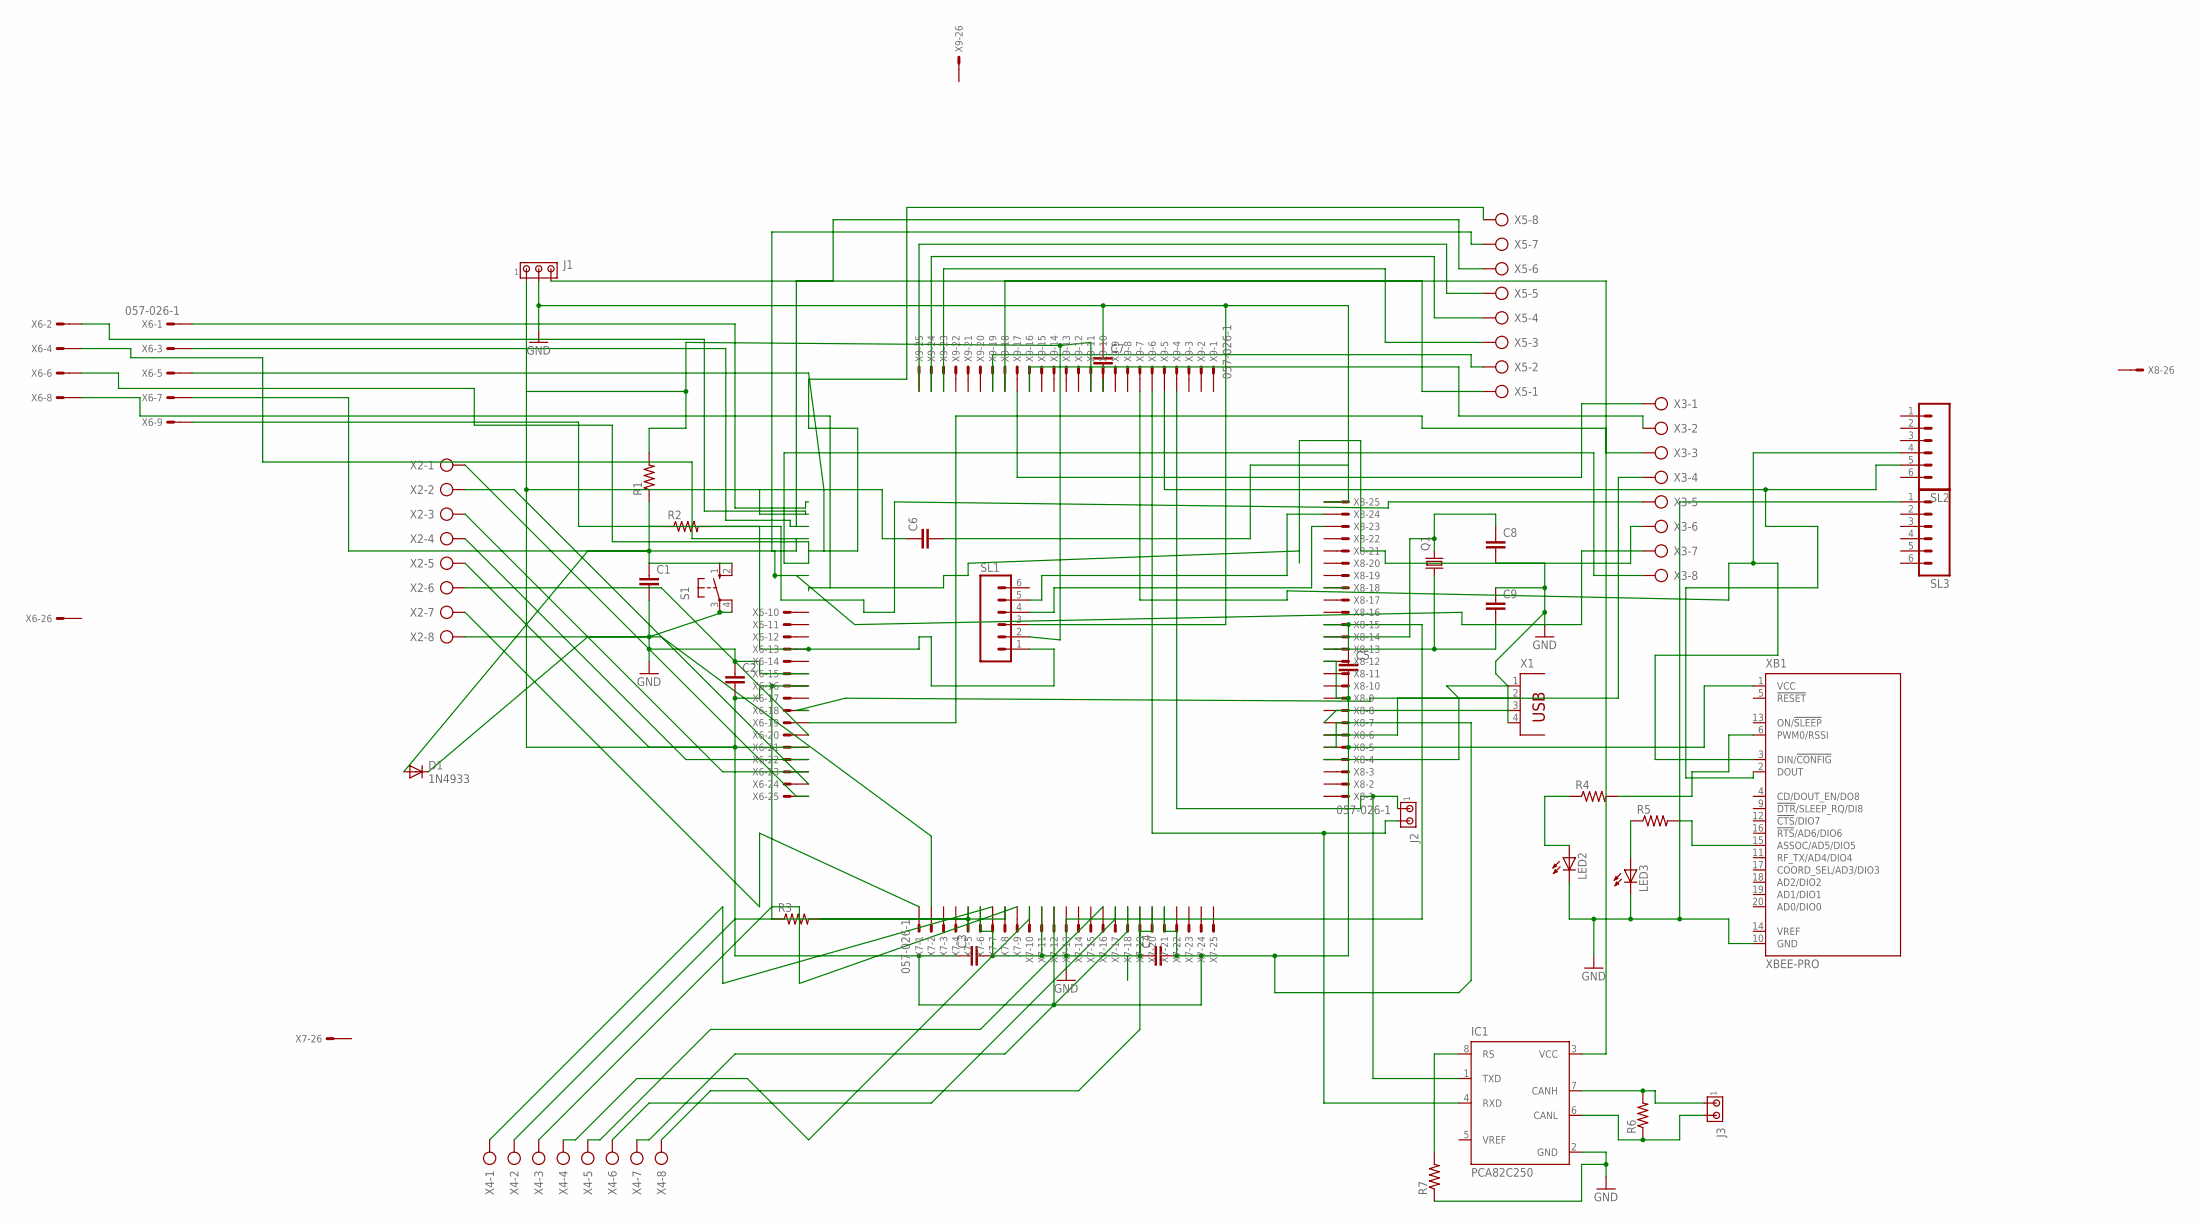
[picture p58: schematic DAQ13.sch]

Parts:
C1, C8, C9: C2,5-3; C2.5-3
C2, C3, C4, C5, C6, C7: C2.5/2; C2.5-2
D1: 1N4933; DO41-10
IC1: PCA82C250; DIL08
J1: MTA03-156; 1X3MTA
J2, J3: MTA02-156; 1X2MTA
LED2, LED3: LED3MM
Q1: CRYSTALHC18U-V; HC18U-V
R1, R2, R3, R4, R5, R6, R7: R-US_0204/7; 0204/7
S1: 10-XX; B3F-10XX
SL1, SL2, SL3: MA06; 06PA
X1: PN87520
X2, X3, X4, X5: AK300/8
X6, X7, X8, X9: 057-026-1
XB1: XBEE-PRO

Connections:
GND: C1.2, C2.1, C3.2, C4.1, C5.1, C6.2, C7.1, C8.2, C9.1, D1.C, IC1.2 (GND), J1.2, LED2.K (C), LED3.K (C), R7.1, S1.3, S1.4 (P1), SL1.3, SL3.1, X1.4, X6.15, X7.6, X7.11, X7.20, X8.15, X8.25, XB1.10 (GND)
unnamed: R2.2, SL1.1, X6.13
unnamed: C1.1, D1.A, R1.1, R2.1, S1.1 (S), S1.2 (S1)
unnamed: C2.2, C3.1, C4.2, C5.2, C6.1, J1.1, R1.2, R3.1, SL1.2, X6.2, X6.16, X7.12, X7.21, X8.5, X8.12, X9.11, XB1.1 (VCC)
unnamed: C7.2, X9.10
unnamed: R4.2, XB1.6 (PWM0/RSSI)
unnamed: SL1.4, X8.23
unnamed: SL1.5, X8.24
unnamed: C8.1, Q1.2, X8.14
unnamed: C9.2, Q1.1, X8.13
unnamed: R5.2, XB1.15 (ASSOC/AD5/DIO5)
unnamed: LED3.A, R5.1
unnamed: LED2.A, R4.1
unnamed: X4.7, X7.18
unnamed: X4.5, X7.16
unnamed: X1.1, X8.4
unnamed: X1.2, X8.6
unnamed: X1.3, X8.7
unnamed: X4.6, X7.17
unnamed: X2.1, X6.25
unnamed: X2.2, X6.24
unnamed: X2.3, X6.23
unnamed: X2.4, X6.22
unnamed: X2.5, X6.21
unnamed: X2.6, X6.20
unnamed: X2.7, X7.1
unnamed: X2.8, X7.2
unnamed: X4.1, X7.7
unnamed: X4.2, X7.8
unnamed: X4.3, X7.9
unnamed: X4.4, X7.10
unnamed: X4.8, X7.19
unnamed: X3.8, X6.6
unnamed: X3.7, X6.7
unnamed: X5.7, X6.4
unnamed: X3.5, X6.9
unnamed: X3.4, X6.18
unnamed: X3.3, X6.19
unnamed: X3.2, X9.16
unnamed: X3.1, X9.17
unnamed: X5.1, X9.18
unnamed: X5.2, X9.19
unnamed: X5.3, X9.23
unnamed: X5.4, X9.24
unnamed: X5.5, X9.25
unnamed: X3.6, X6.8
unnamed: X5.8, X6.5
unnamed: IC1.7 (CANH), J3.1, R6.2
unnamed: IC1.8 (RS), R7.2
unnamed: IC1.1 (TXD), J2.1, X9.4
unnamed: IC1.6 (CANL), J3.2, R6.1
unnamed: IC1.4 (RXD), J2.2, X9.6
unnamed: IC1.3 (VCC), J1.3
unnamed: SL2.5, X9.5, XB1.2 (DOUT)
unnamed: SL2.4, X9.7, XB1.3 (DIN/!CONFIG)
unnamed: X5.6, X6.3
unnamed: R3.2, X7.5

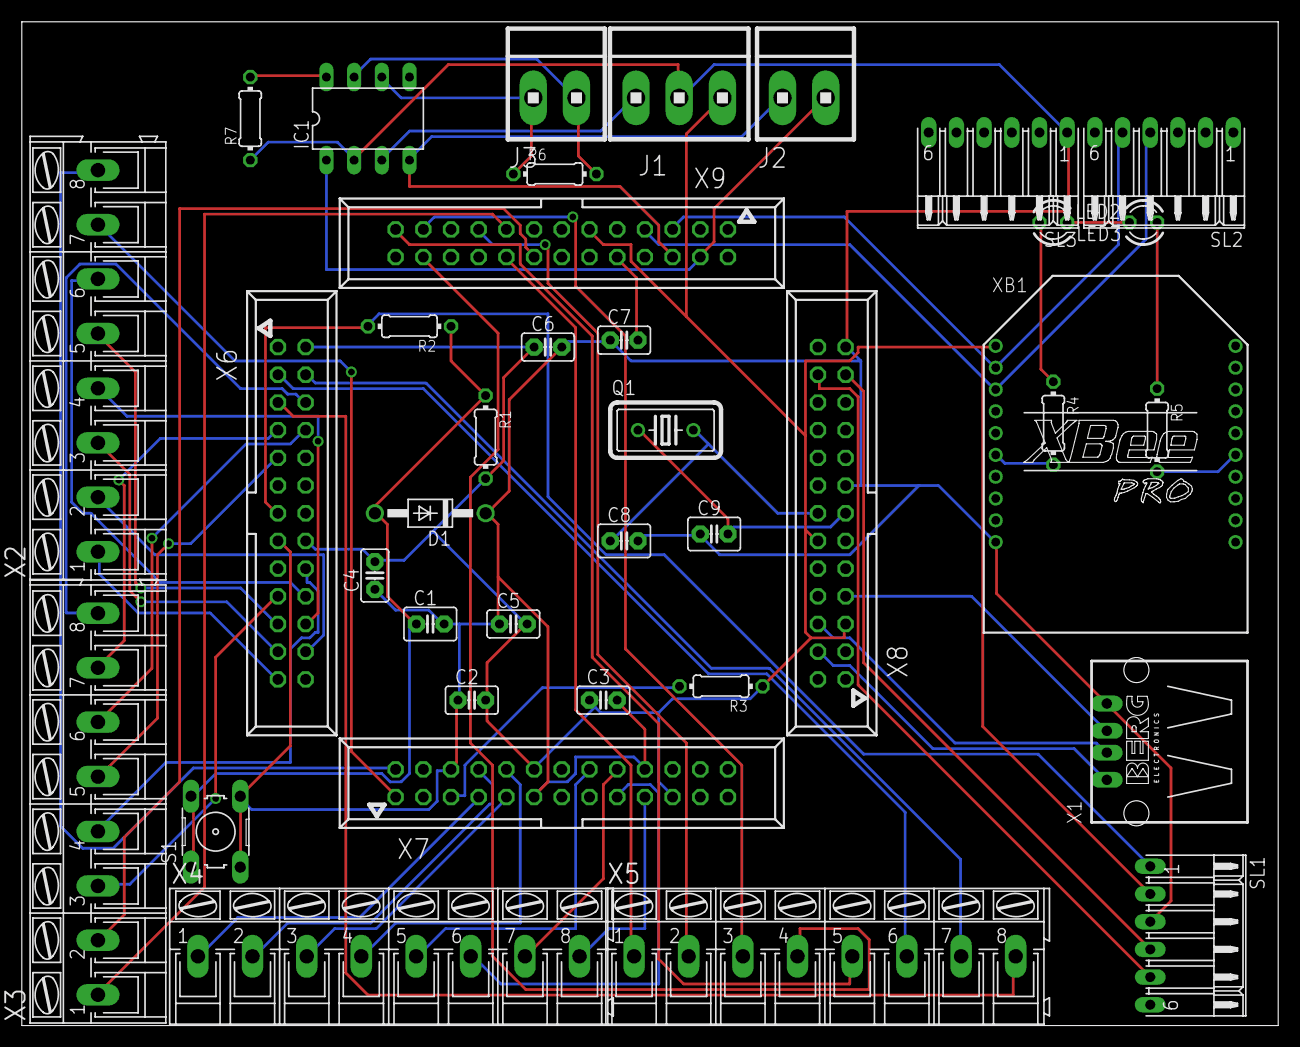
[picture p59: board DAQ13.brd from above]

Board: 2 copper layers, 115.2 x 92.1 mm, 38 parts (0 on the bottom side), 57 nets.

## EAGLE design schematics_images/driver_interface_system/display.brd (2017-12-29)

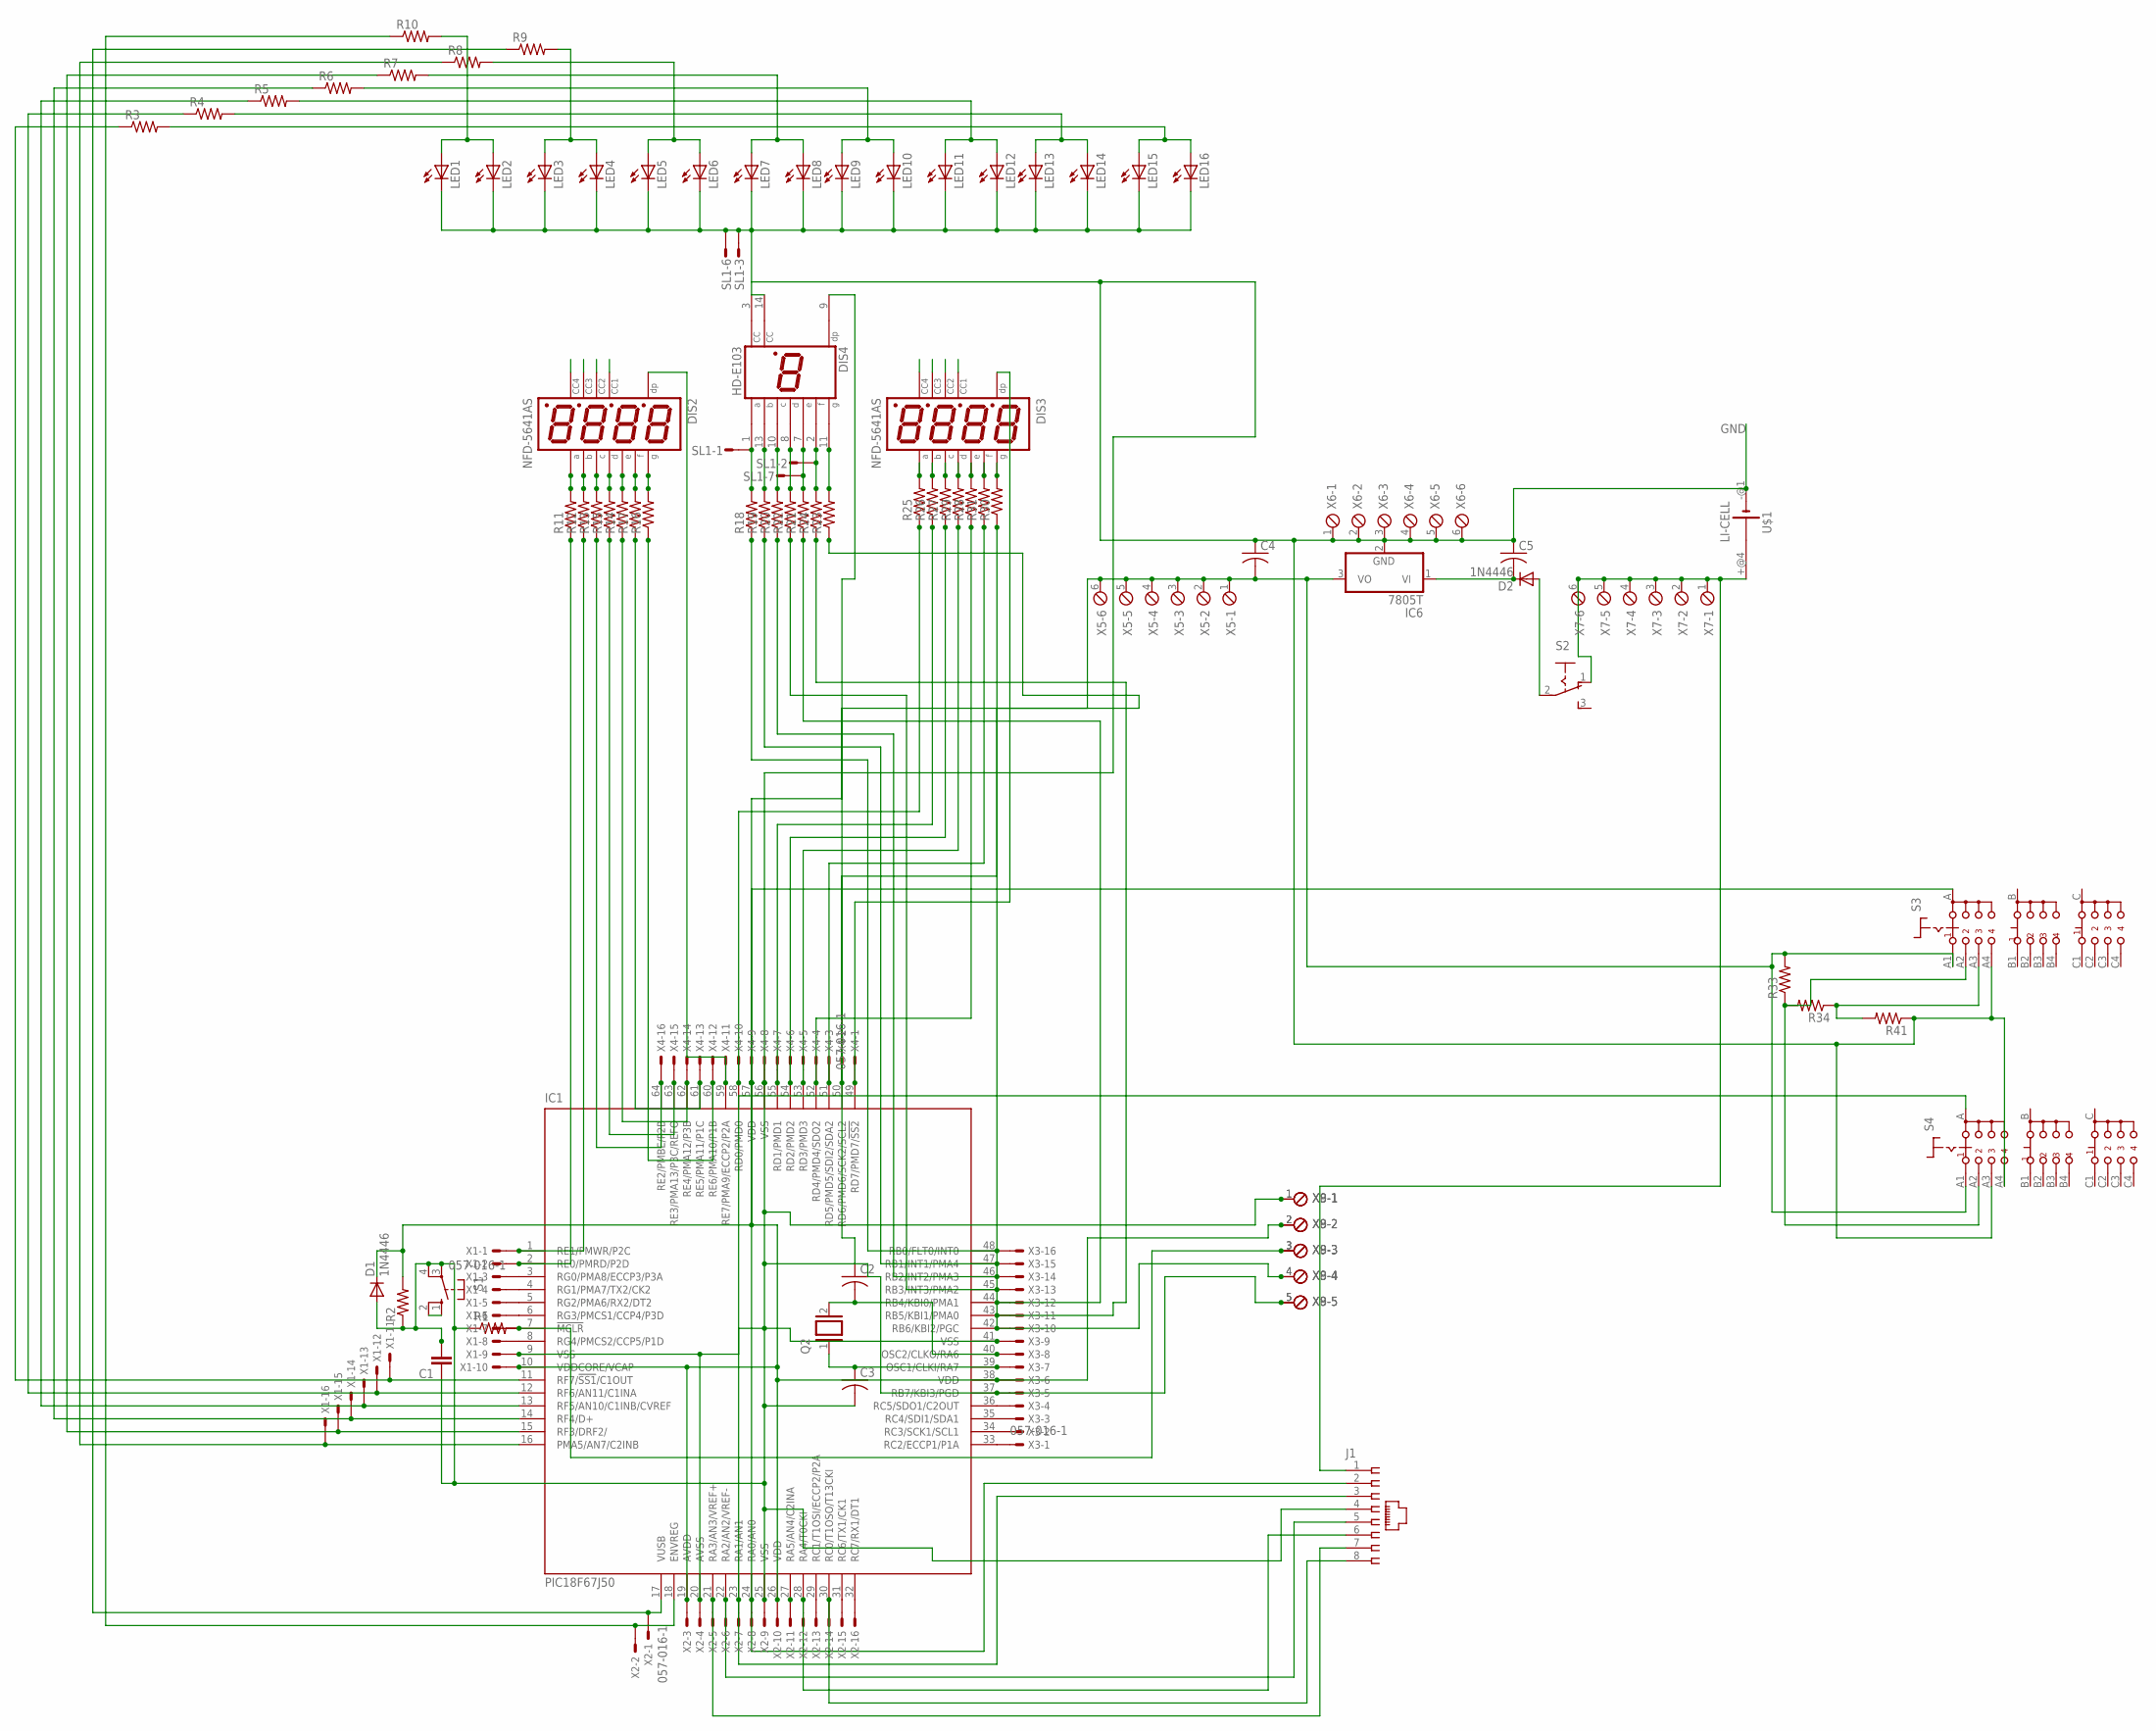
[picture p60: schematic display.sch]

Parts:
C1: C2.5/2; C2.5-2
C2, C3, C4, C5: C-US025-024X044; C025-024X044
D1, D2: 1N4446; DO35-10
DIS2, DIS3: NFD-5641AS; NFD-5641
DIS4: HD-E103; HDSP-I
IC1: PIC18F67J50; TQFP64-10X10
IC6: 7805T; TO220H
J1: 520244-4
LED1, LED2, LED3, LED4, LED5, LED6, LED7, LED8, LED9, LED10, LED11, LED12, LED13, LED14, LED15, LED16: LED5MM
Q2: XTAL/S; QS
R1, R2: R-US_0309/10; 0309/10
R3, R4, R5, R6, R7, R8, R9, R10, R11, R12, R13, R14, R15, R16, R17, R18, R19, R20, R21, R22, R23, R24, R25, R26, R27, R28, R29, R30, R31, R33, R34, R41: R-US_0207/10; 0207/10
S1: 10-XX; B3F-10XX
S2: 255SB
S3, S4: CK103X04
SL1: M07S; 07P
U$1: LI-CELL
X1, X2, X3, X4: 057-016-1
X5, X6, X7: MPT6; 6POL254
X8, X9: MPT5; 5POL254

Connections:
GND: C1.1, C1.2, C2.1, C3.2, C4.1, C5.1, D1.A, DIS4.3 (CC), DIS4.14 (CC), IC1.9 (VSS), IC1.20 (AVSS), IC1.25 (VSS), IC1.41 (VSS), IC1.56 (VSS), IC6.2 (GND), J1.4, LED1.K (C), LED2.K (C), LED3.K (C), LED4.K (C), LED5.K (C), LED6.K (C), LED7.K (C), LED8.K (C), LED9.K (C), LED10.K (C), LED11.K (C), LED12.K (C), LED13.K (C), LED14.K (C), LED15.K (C), LED16.K (C), R1.1, R2.1, R41.1, S1.3, S1.4 (P1), S3.A4, S4.A3, S4.A4, SL1.3, SL1.6, U$1.-@1 (-), X1.9, X2.4, X2.9, X3.9, X4.8, X6.1, X6.2, X6.3, X6.4, X6.5, X6.6, X8.1, X9.1
L1: DIS2.P$12
L2: DIS2.P$9
L3: DIS2.P$8
L4: DIS2.P$6
unnamed: IC1.7 (!MCLR), R1.2, X1.7, X8.3, X9.3
unnamed: IC1.18 (ENVREG), R10.1, X2.2
unnamed: IC1.17 (VUSB), R9.1, X2.1
unnamed: IC1.16 (PMA5/AN7/C2INB), R8.1, X1.16
unnamed: IC1.15 (RF3/DRF2/), R7.1, X1.15
unnamed: IC1.14 (RF4/D+), R6.1, X1.14
unnamed: IC1.13 (RF5/AN10/C1INB/CVREF), R5.1, X1.13
unnamed: IC1.12 (RF6/AN11/C1INA), R4.1, X1.12
unnamed: IC1.11 (RF7/!SS1!/C1OUT), R3.1, X1.11
unnamed: IC1.3 (RG0/PMA8/ECCP3/P3A), X1.3
unnamed: DIS2.P$11, R11.2
unnamed: DIS4.2 (F), R24.2, SL1.2
unnamed: IC1.2 (RE0/PMRD/P2D), R11.1, X1.2
unnamed: DIS2.P$4, R13.2
unnamed: DIS3.P$11, R25.2
unnamed: DIS2.P$1, R14.2
unnamed: DIS4.7 (E), R21.2, SL1.7
unnamed: DIS2.P$2, R15.2
unnamed: DIS2.P$5, R16.2
unnamed: IC1.4 (RG1/PMA7/TX2/CK2), X1.4
unnamed: IC1.28 (RA4/T0CKI), J1.6, X2.12
unnamed: IC1.5 (RG2/PMA6/RX2/DT2), X1.5
unnamed: IC1.6 (RG3/PMCS1/CCP4/P3D), X1.6
unnamed: IC1.1 (RE1/PMWR/P2C), R12.1, X1.1
unnamed: LED1.A, LED2.A, R10.2
unnamed: IC1.8 (RG4/PMCS2/CCP5/P1D), X1.8
unnamed: C2.2, IC1.40 (OSC2/CLKO/RA6), Q2.2, X3.8
unnamed: C3.1, IC1.39 (OSC1/CLKI/RA7), Q2.1, X3.7
unnamed: R34.1, R41.2, S3.A3
unnamed: R24.1, X3.11
unnamed: IC1.27 (RA5/AN4/C2INA), X2.11
unnamed: IC1.29 (RC1/T1OSI/ECCP2/P2A), X2.13
unnamed: IC1.31 (RC6/TX1/CK1), X2.15
unnamed: IC1.32 (RC7/RX1/DT1), X2.16
unnamed: IC1.33 (RC2/ECCP1/P1A), X3.1
unnamed: DIS2.P$10, R17.2
unnamed: IC1.34 (RC3/SCK1/SCL1), X3.2
unnamed: DIS2.P$7, R12.2
unnamed: IC1.35 (RC4/SDI1/SDA1), X3.3
unnamed: IC1.64 (RE2/PMBE/P2B), R13.1, X4.16
unnamed: IC1.21 (RA3/AN3/VREF+), J1.7, X2.5
unnamed: IC1.62 (RE4/PMA12/P3B), R14.1, X4.14
unnamed: IC1.22 (RA2/AN2/VREF-), J1.5, X2.6
unnamed: IC1.60 (RE6/PMA10/P1B), R16.1, X4.12
unnamed: DIS4.1 (A), R18.2, SL1.1
unnamed: DIS4.10 (C), R20.2
unnamed: DIS3.P$4, R27.2
unnamed: DIS4.8 (D), R22.2
unnamed: IC1.36 (RC5/SDO1/C2OUT), X3.4
unnamed: IC1.23 (RA1/AN1), J1.3, S4.A, X2.7
unnamed: IC1.30 (RC0/T1OSO/T13CKI), J1.8, X2.14
unnamed: DIS4.9 (DP), IC1.37 (RB7/KBI3/PGD), X3.5, X8.5, X9.5
unnamed: IC1.45 (RB3/INT3/PMA2), R22.1, X3.13
unnamed: IC1.47 (RB1/INT1/PMA4), R19.1, X3.15
unnamed: DIS3.P$3, IC1.49 (RD7/PMD7/!SS2), X4.1
unnamed: IC1.53 (RD3/PMD3), R29.1, X4.5
unnamed: IC1.55 (RD1/PMD1), R26.1, X4.7
unnamed: IC1.51 (RD5/PMD5/SDI2/SDA2), R31.1, X4.3
unnamed: DIS2.P$3, IC1.59 (RE7/PMA9/ECCP2/P2A), X4.11
unnamed: IC1.63 (RE3/PMA13/P3C/REFO), R15.1, X4.15
unnamed: C5.2, D2.C, IC6.1 (VI)
unnamed: LED3.A, LED4.A, R9.2
unnamed: LED5.A, LED6.A, R8.2
unnamed: LED7.A, LED8.A, R7.2
unnamed: D2.A, S2.2
unnamed: LED9.A, LED10.A, R6.2
unnamed: LED11.A, LED12.A, R5.2
unnamed: LED13.A, LED14.A, R4.2
unnamed: LED15.A, LED16.A, R3.2
unnamed: S1.1 (S), S1.2 (S1)
unnamed: J1.1, S2.1 (O), U$1.+@4 (+), X7.1, X7.2, X7.3, X7.4, X7.5, X7.6
unnamed: DIS4.11 (G), R23.2
unnamed: DIS3.P$1, R28.2
unnamed: DIS4.13 (B), R19.2
unnamed: DIS3.P$2, R29.2
unnamed: DIS3.P$5, R30.2
unnamed: DIS3.P$10, R31.2
unnamed: DIS3.P$7, R26.2
unnamed: IC1.58 (RD0/PMD0), R25.1, X4.10
unnamed: IC1.54 (RD2/PMD2), R27.1, X4.6
unnamed: IC1.52 (RD4/PMD4/SDO2), R28.1, X4.4
unnamed: IC1.50 (RD6/PMD6/SCK2/SCL2), R30.1, X4.2
unnamed: IC1.48 (RB0/FLT0/INT0), R18.1, X3.16
unnamed: IC1.46 (RB2/INT2/PMA3), R20.1, X3.14
unnamed: IC1.44 (RB4/KBI0/PMA1), R21.1, X3.12
unnamed: IC1.42 (RB6/KBI2/PGC), IC1.43 (RB5/KBI1/PMA0), R23.1, X3.10, X8.4, X9.4
unnamed: IC1.61 (RE5/PMA11/P1C), R17.1, X4.13
unnamed: R33.1, R34.2, S3.A2, S4.A2
unnamed: C4.2, D1.C, IC1.10 (VDDCORE/VCAP), IC1.19 (AVDD), IC1.26 (VDD), IC1.38 (VDD), IC6.3 (VO), R2.2, R33.2, S3.A1, S4.A1, X1.10, X2.3, X2.10, X3.6, X4.9, X5.1, X5.2, X5.3, X5.4, X5.5, X5.6, X8.2, X9.2
unnamed: IC1.24 (RA0/AN0), IC1.57 (VDD), J1.2, S3.A, X2.8
R1: DIS3.P$12
R2: DIS3.P$9
R3: DIS3.P$8
R4: DIS3.P$6

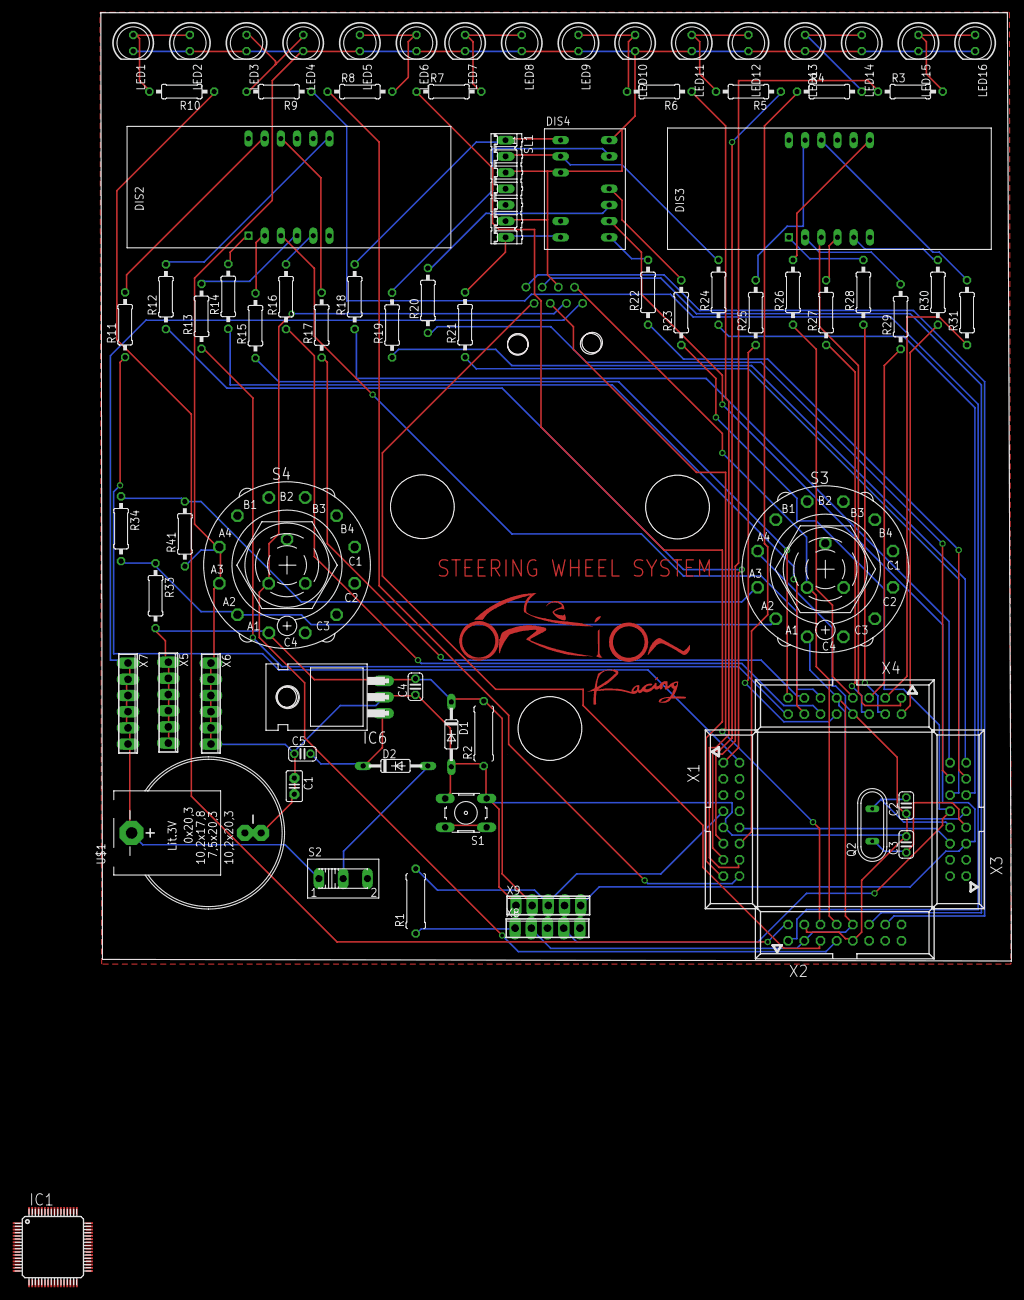
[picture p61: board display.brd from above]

Board: 2 copper layers, 142.9 x 148.8 mm, 79 parts (1 on the bottom side), 91 nets.

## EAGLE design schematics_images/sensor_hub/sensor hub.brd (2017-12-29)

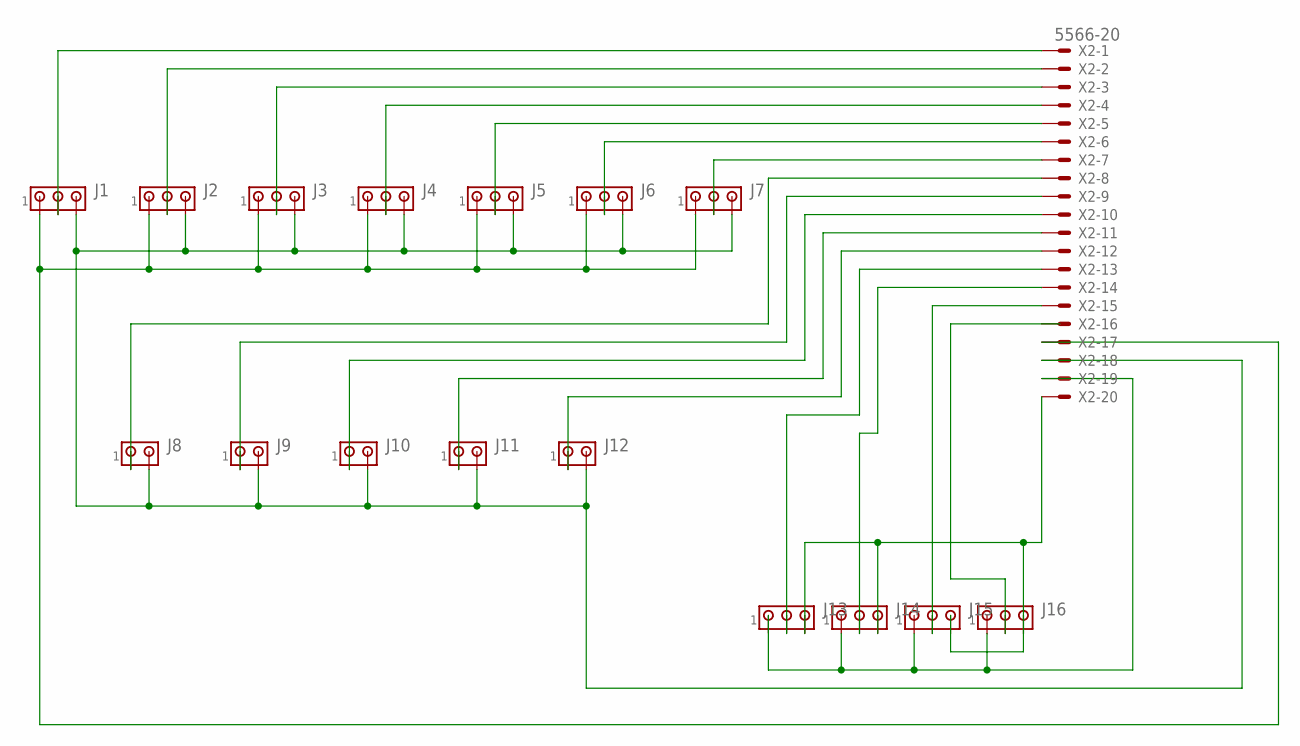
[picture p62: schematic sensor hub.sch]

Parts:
J1, J2, J3, J4, J5, J6, J7, J13, J14, J15, J16: MTA03-156; 1X3MTA
J8, J9, J10, J11, J12: MTA02-156; 1X2MTA
X2: 5566-20

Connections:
unnamed: J13.2, X2.13
unnamed: J14.2, X2.14
unnamed: J15.2, X2.15
unnamed: J5.2, X2.5
unnamed: J6.2, X2.6
unnamed: J11.1, X2.11
unnamed: J12.1, X2.12
unnamed: J14.1, J15.1, J16.1, X2.19
unnamed: J13.3, J14.3, J16.3, X2.20
unnamed: J1.2, X2.1
unnamed: J2.2, X2.2
unnamed: J3.2, X2.3
unnamed: J4.2, X2.4
unnamed: J7.2, X2.7
unnamed: J8.1, X2.8
unnamed: J9.1, X2.9
unnamed: J10.1, X2.10
unnamed: J1.3, J2.3, J3.3, J4.3, J5.3, J6.3, J7.3, J8.2, J9.2, J10.2, J11.2, J12.2, X2.18
unnamed: J1.1, J2.1, J3.1, J4.1, J5.1, J6.1, J7.1, X2.17

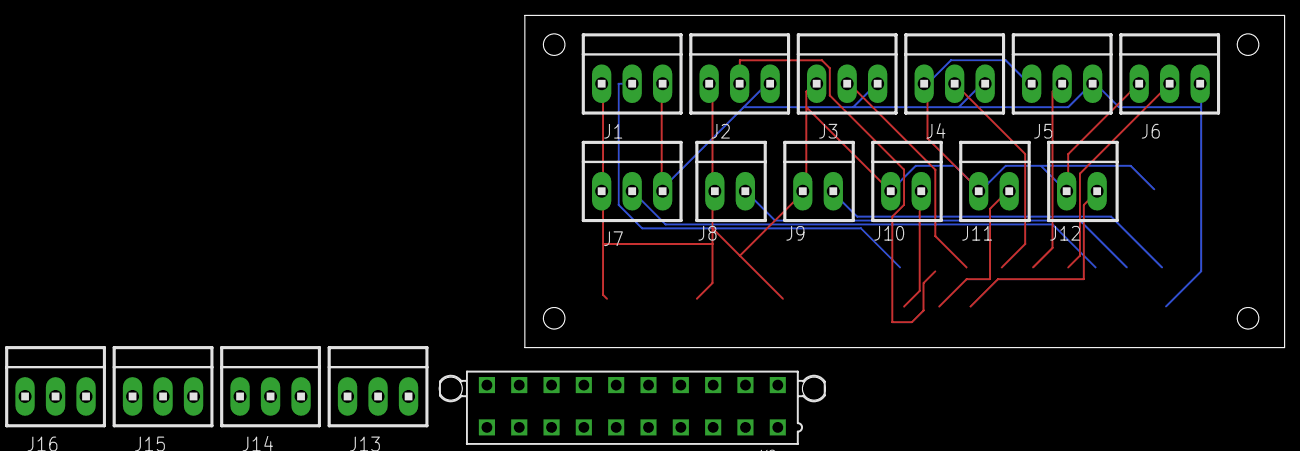
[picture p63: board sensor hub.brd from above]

Board: 2 copper layers, 98.7 x 43.2 mm, 17 parts (0 on the bottom side), 19 nets.

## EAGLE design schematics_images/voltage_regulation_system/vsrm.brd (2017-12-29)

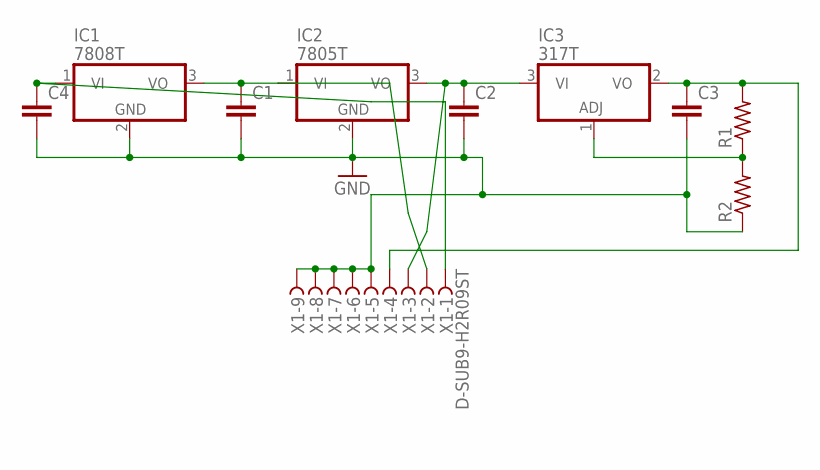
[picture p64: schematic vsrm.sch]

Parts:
C1, C2, C3, C4: C2.5/4; C2.5-4
IC1: 7808T; TO220H
IC2: 7805T; TO220H
IC3: 317T; TO220H
R1, R2: R-US_0204/7; 0204/7
X1: D-SUB9-H2R09ST; H2R09ST

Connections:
GND: C1.2, C2.2, C3.2, C4.2, IC1.2 (GND), IC2.2 (GND), R2.1, X1.5, X1.6, X1.7, X1.8, X1.9
unnamed: C1.1, IC1.3 (VO), IC2.1 (VI), X1.2
unnamed: C3.1, IC3.2 (VO), R1.2, X1.4
unnamed: C2.1, IC2.3 (VO), IC3.3 (VI), X1.3
unnamed: C4.1, IC1.1 (VI), X1.1
unnamed: IC3.1 (ADJ), R1.1, R2.2

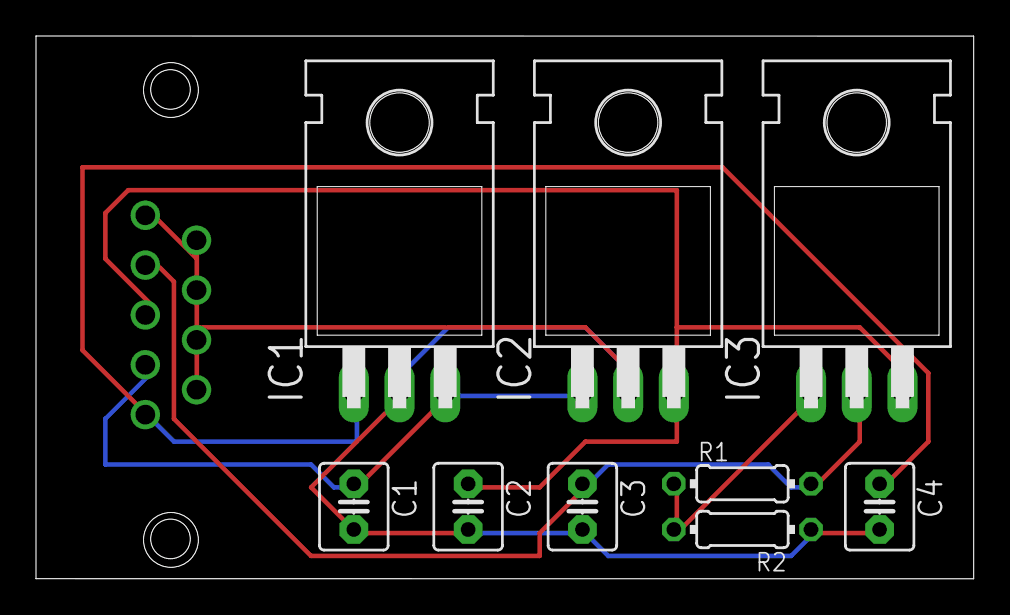
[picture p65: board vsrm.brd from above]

Board: 2 copper layers, 52.1 x 30.2 mm, 10 parts (1 on the bottom side), 6 nets.

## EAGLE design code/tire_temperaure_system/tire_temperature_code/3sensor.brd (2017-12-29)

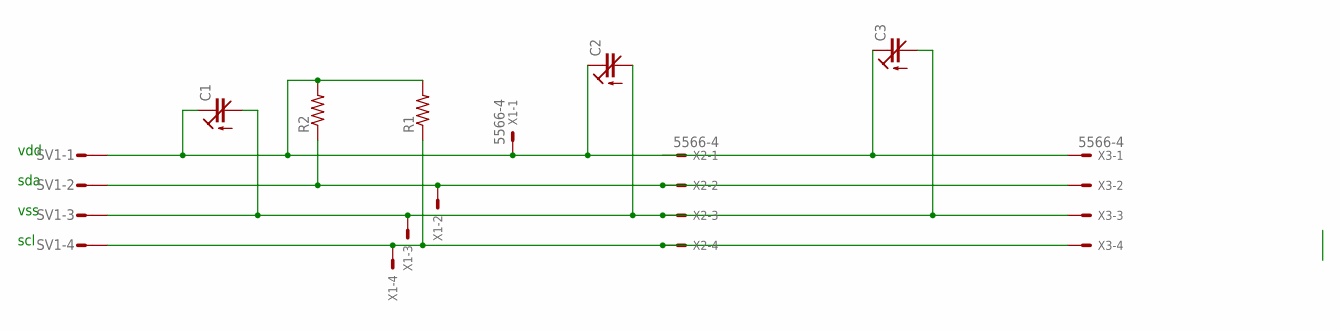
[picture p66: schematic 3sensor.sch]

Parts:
C1, C2, C3: C-TRIMM3008; 3008
R1, R2: R-US_0207/12; 0207/12
SV1: L04P
X1, X2, X3: 5566-4

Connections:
unnamed: R1.1, SV1.4, X1.4, X2.4, X3.4
unnamed: R2.1, SV1.2, X1.2, X2.2, X3.2
VDD: C1.+ (E), C2.+ (E), C3.+ (E), R1.2, R2.2, SV1.1, X1.1, X2.1, X3.1
VSS: C1.- (A), C2.- (A), C3.- (A), SV1.3, X1.3, X2.3, X3.3

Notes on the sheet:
vdd
sda
vss
scl

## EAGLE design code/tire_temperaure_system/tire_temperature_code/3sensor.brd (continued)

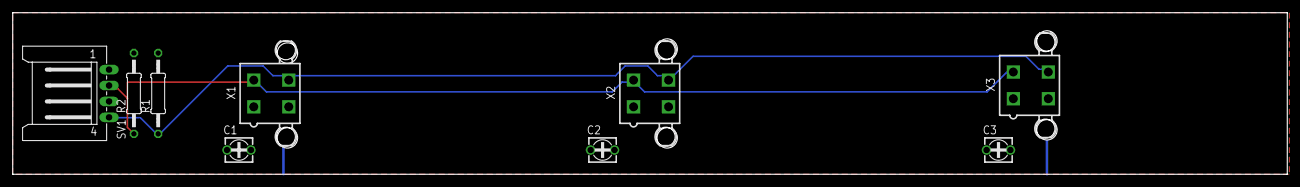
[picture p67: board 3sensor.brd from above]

Board: 2 copper layers, 200.3 x 25.4 mm, 9 parts (0 on the bottom side), 4 nets.

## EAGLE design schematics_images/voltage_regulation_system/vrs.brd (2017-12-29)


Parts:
H1: MOUNT-PAD-ROUND5.5; 5,5-PAD
IC1, IC2, IC3, IC4, IC5, IC6: 7805TV; TO220V
J1: MTA04-156; 1X4MTA
LED1, LED2, LED3, LED4, LED5, LED6: LED3MM
Q1, Q2, Q3: BC547A; TO92
Q4: IRF3704L-V; TO262-V
R1, R2, R3, R4, R5, R6, R7, R8, R9, R10, R11, R12, R13, R14, R15, R16, R17: R-US_0207/10; 0207/10
SV1, SV2: MT6-8Y
T1, T2, T3: -PNP-TO92L; TO92L
X1, X2, X4, X6: AK300/2
X3, X5: D-SUB9-H2R09ST; H2R09ST
X12: D-SUB9-H3M09RA; H3M09RA

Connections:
GND2: H1.B5,5, IC1.2 (GND), IC2.2 (GND), IC3.2 (GND), IC4.2 (GND), IC5.2 (GND), IC6.2 (GND), LED1.K (C), LED3.K (C), LED5.K (C), Q1.1 (E), Q2.1 (E), Q3.1 (E), Q4.1 (G), R4.1, R9.1, R14.1, R17.2, X2.2, X3.5, X3.6, X3.7, X3.8, X3.9, X5.5, X5.6, X5.7, X5.8, X5.9, X6.2
unnamed: Q2.2 (B), R7.1
unnamed: Q2.3 (C), R6.1
unnamed: R6.2, T2.2 (B)
unnamed: Q1.2 (B), R2.1
unnamed: Q1.3 (C), R1.1
unnamed: R1.2, T1.2 (B)
unnamed: Q4.2 (D), X2.1
unnamed: LED1.A, R5.1
unnamed: J1.1, J1.2, J1.3, J1.4, LED2.K (C), R2.2, R4.2, R5.2, T1.3 (C), X12.1, X12.2, X12.3, X12.4, X12.5
unnamed: LED2.A, R3.2
unnamed: LED4.K (C), R7.2, R9.2, R10.2, SV1.1, SV1.2, SV1.3, SV1.4, SV1.5, SV1.6, SV1.7, SV1.8, T2.3 (C)
unnamed: X4.2, X12.7
unnamed: LED3.A, R10.1
unnamed: R16.2, R17.1, X12.9
unnamed: LED4.A, R8.2
unnamed: Q3.2 (B), R12.1
unnamed: Q3.3 (C), R11.1
unnamed: R11.2, T3.2 (B)
unnamed: LED6.K (C), R12.2, R14.2, R15.2, SV2.1, SV2.2, SV2.3, SV2.4, SV2.5, SV2.6, SV2.7, SV2.8, T3.3 (C)
unnamed: X4.1, X12.6
unnamed: LED5.A, R15.1
unnamed: X1.1, X12.8
unnamed: LED6.A, R13.2
unnamed: R3.1, T1.1 (E), X3.2, X5.2
unnamed: R8.1, T2.1 (E), X3.3, X5.3
unnamed: R13.1, T3.1 (E), X3.4, X5.4
unnamed: IC1.1 (VI), IC2.1 (VI), IC3.1 (VI), IC4.1 (VI), IC5.1 (VI), IC6.1 (VI), Q4.3 (S), R16.1, X1.2, X3.1, X5.1
unnamed: IC1.3 (VO), IC2.3 (VO), IC3.3 (VO), IC4.3 (VO), IC5.3 (VO), IC6.3 (VO), X6.1


Board: 2 copper layers, 104.2 x 59.7 mm, 47 parts (0 on the bottom side), 29 nets.

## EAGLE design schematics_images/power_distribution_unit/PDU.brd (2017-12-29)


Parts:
H1, H2: MOUNT-PAD-SQUARE5.0; 5,0-PAD-SQUARE
H4, H5: MOUNT-PAD-SQUARE5.5; 5,5-PAD-SQUARE
IC1: BTS555E3146; TO220-52
Q1, Q2: IRLZ44Z; TO220BH
R1, R2: 100; R1206
SL1: 1; 03P
SM: MOUNT-PAD-SQUARE5.5; 5,5-PAD-SQUARE

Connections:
FANS: Q1.G, R1.1, SL1.3
FIS: Q2.G, R2.1, SL1.2
GND: H4.B5,5, Q1.S, Q2.S, R1.2, R2.2
H1: H1.B5
H2: H2.B5
H5: H5.B5,5
SM: IC1.1 (O1), IC1.5 (O2), SM.B5,5
SMS: IC1.2 (IN), SL1.1



Board: 2 copper layers, 60.6 x 53.8 mm, 11 parts (2 on the bottom side), 5 nets.

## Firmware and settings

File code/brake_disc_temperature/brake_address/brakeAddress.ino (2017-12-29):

#include <i2cmaster.h>

// Pins: Standard: SDA:A4  SCL:A5
//           Mega: SDA:D20 SCL:D21

//byte MLXAddr = 0x5A<<1;           // Default address
//byte MLXAddr = 0;                 // Universal address
  byte MLXAddr = 0x0A<<1;           // New Address: Change this value to wathever you want the new adress of the MLX to be.

void setup(){
  Serial.begin(9600);
  Serial.println("Setup...");
  
  i2c_init();                                // Initialise the i2c bus
  PORTC = (1 << PORTC4) | (1 << PORTC5);   // Enable pullups resistors (uncomment for std arduinos)
  //PORTD = (1 << PORTD1) | (1 << PORTD0);     // Enable pullups resistors (uncomment for arduino MEGA)
  
  delay(5000);                    // Wait to allow serial connection
  ReadAddr(0);                    // Read current address bytes
  ChangeAddr(MLXAddr>>1, 0x00);   // Change address to new value
  ReadAddr(0);                    // Read address bytes
  Serial.println("Manually cycle power the MLX, you have 10 seconds.");
  //delay(10000);                    // Cycle power to MLX during this pause
  Serial.println("Cycle power delay expired.");
  delay(2000);                     // Additionnal delay buffer
  Serial.println("Testing temperature reading on universal address.");
  ReadTemp(0);                    // Read temperature using default address
  Serial.println("Testing temperature reading on new address.");
  ReadTemp(MLXAddr);              // Read temperature using new address
  Serial.println("Done");
}

void loop(){ 
  delay(1000);                    // wait a second 
}


word ChangeAddr(byte NewAddr1, byte NewAddr2) {

  Serial.println("> Change address");

  i2c_start_wait(0 + I2C_WRITE);    //send start condition and write bit
  i2c_write(0x2E);                  //send command for device to return address
  i2c_write(0x00);                  // send low byte zero to erase
  i2c_write(0x00);                  //send high byte zero to erase
  if (i2c_write(0x6F) == 0) {
    i2c_stop();                     //Release bus, end transaction
    Serial.println("  Data erased.");
  }
  else {
    i2c_stop();                     //Release bus, end transaction
    Serial.println("  Failed to erase data");
    return -1;
  }

  Serial.print("  Writing data: ");
  Serial.print(NewAddr1, HEX);
  Serial.print(", ");
  Serial.println(NewAddr2, HEX);

  for (int a = 0; a != 256; a++) {
    i2c_start_wait(0 + I2C_WRITE);  //send start condition and write bit
    i2c_write(0x2E);                //send command for device to return address
    i2c_write(NewAddr1);            // send low byte zero to erase
    i2c_write(NewAddr2);            //send high byte zero to erase
    if (i2c_write(a) == 0) {
      i2c_stop();                   //Release bus, end transaction
      delay(100);                   // then wait 10ms
      Serial.print("Found correct CRC: 0x");
      Serial.println(a, HEX);
      return a;
    }
  }
  i2c_stop();                       //Release bus, end transaction
  Serial.println("Correct CRC not found");
  return -1;
}

void ReadAddr(byte Address) {

  Serial.println("> Read address");

  Serial.print("  MLX address: ");
  Serial.print(Address, HEX);
  Serial.print(", Data: ");

  i2c_start_wait(Address + I2C_WRITE);  //send start condition and write bit
  i2c_write(0x2E);                  //send command for device to return address
  i2c_rep_start(Address + I2C_READ);
  
  Serial.print(i2c_readAck(), HEX); //Read 1 byte and then send ack
  Serial.print(", ");
  Serial.print(i2c_readAck(), HEX); //Read 1 byte and then send ack
  Serial.print(", ");
  Serial.println(i2c_readNak(), HEX);
  i2c_stop();
}

float ReadTemp(byte Address) {
  int data_low = 0;
  int data_high = 0;
  int pec = 0;

  Serial.println("> Read temperature");

  Serial.print("  MLX address: ");
  Serial.print(Address, HEX);
  Serial.print(", ");

  i2c_start_wait(Address + I2C_WRITE);
  i2c_write(0x07);                  // Address of temp bytes
  
  // read
  i2c_rep_start(Address + I2C_READ);
  data_low = i2c_readAck();         //Read 1 byte and then send ack
  data_high = i2c_readAck();        //Read 1 byte and then send ack
  pec = i2c_readNak();
  i2c_stop();
  
  //This converts high and low bytes together and processes temperature, MSB is a error bit and is ignored for temps
  float Temperature = 0x0000;       // zero out the data
  
  // This masks off the error bit of the high byte, then moves it left 8 bits and adds the low byte.
  Temperature = (float)(((data_high & 0x007F) << 8) + data_low);
  Temperature = (Temperature * 0.02) - 273.16;
  
  Serial.print(Temperature);
  Serial.println(" C");
  return Temperature;
}

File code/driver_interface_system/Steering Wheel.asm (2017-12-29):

_seg7:

;Steering Wheel.c,7 :: 		int seg7(int num)
;Steering Wheel.c,9 :: 		int val[]={0x3f,0x06,0x5b,0x4f,0x66,0x6D,0x7D,0x07,0x7F,0x6F,0x77,0x7C,0x39,0x5E,0x79,0x71};
	MOVLW       ?ICSseg7_val_L0+0
	MOVWF       TBLPTRL 
	MOVLW       hi_addr(?ICSseg7_val_L0+0)
	MOVWF       TBLPTRH 
	MOVLW       higher_addr(?ICSseg7_val_L0+0)
	MOVWF       TBLPTRU 
	MOVLW       seg7_val_L0+0
	MOVWF       FSR1L 
	MOVLW       hi_addr(seg7_val_L0+0)
	MOVWF       FSR1H 
	MOVLW       32
	MOVWF       R0 
	MOVLW       1
	MOVWF       R1 
	CALL        ___CC2DW+0, 0
;Steering Wheel.c,10 :: 		return(val[num]);
	MOVF        FARG_seg7_num+0, 0 
	MOVWF       R0 
	MOVF        FARG_seg7_num+1, 0 
	MOVWF       R1 
	RLCF        R0, 1 
	BCF         R0, 0 
	RLCF        R1, 1 
	MOVLW       seg7_val_L0+0
	ADDWF       R0, 0 
	MOVWF       FSR0L 
	MOVLW       hi_addr(seg7_val_L0+0)
	ADDWFC      R1, 0 
	MOVWF       FSR0H 
	MOVF        POSTINC0+0, 0 
	MOVWF       R0 
	MOVF        POSTINC0+0, 0 
	MOVWF       R1 
;Steering Wheel.c,11 :: 		}
	RETURN      0
; end of _seg7

_gear:

;Steering Wheel.c,13 :: 		int gear(int num)
;Steering Wheel.c,15 :: 		int val[]={0xFE,0x06,0xDA,0xCE,0x66,0xEC,0xFC,0x86,0xFE,0xEE};
	MOVLW       ?ICSgear_val_L0+0
	MOVWF       TBLPTRL 
	MOVLW       hi_addr(?ICSgear_val_L0+0)
	MOVWF       TBLPTRH 
	MOVLW       higher_addr(?ICSgear_val_L0+0)
	MOVWF       TBLPTRU 
	MOVLW       gear_val_L0+0
	MOVWF       FSR1L 
	MOVLW       hi_addr(gear_val_L0+0)
	MOVWF       FSR1H 
	MOVLW       20
	MOVWF       R0 
	MOVLW       1
	MOVWF       R1 
	CALL        ___CC2DW+0, 0
;Steering Wheel.c,16 :: 		return(val[num]);
	MOVF        FARG_gear_num+0, 0 
	MOVWF       R0 
	MOVF        FARG_gear_num+1, 0 
	MOVWF       R1 
	RLCF        R0, 1 
	BCF         R0, 0 
	RLCF        R1, 1 
	MOVLW       gear_val_L0+0
	ADDWF       R0, 0 
	MOVWF       FSR0L 
	MOVLW       hi_addr(gear_val_L0+0)
	ADDWFC      R1, 0 
	MOVWF       FSR0H 
	MOVF        POSTINC0+0, 0 
	MOVWF       R0 
	MOVF        POSTINC0+0, 0 
	MOVWF       R1 
;Steering Wheel.c,17 :: 		}
	RETURN      0
; end of _gear

_segl:

;Steering Wheel.c,19 :: 		segl()
;Steering Wheel.c,21 :: 		th=value/1000;
	MOVLW       232
	MOVWF       R4 
	MOVLW       3
	MOVWF       R5 
	MOVF        _value+0, 0 
	MOVWF       R0 
	MOVF        _value+1, 0 
	MOVWF       R1 
	CALL        _Div_16x16_S+0, 0
	MOVF        R0, 0 
	MOVWF       _th+0 
;Steering Wheel.c,22 :: 		h=value/100%10;
	MOVLW       100
	MOVWF       R4 
	MOVLW       0
	MOVWF       R5 
	MOVF        _value+0, 0 
	MOVWF       R0 
	MOVF        _value+1, 0 
	MOVWF       R1 
	CALL        _Div_16x16_S+0, 0
	MOVLW       10
	MOVWF       R4 
	MOVLW       0
	MOVWF       R5 
	CALL        _Div_16x16_S+0, 0
	MOVF        R8, 0 
	MOVWF       R0 
	MOVF        R9, 0 
	MOVWF       R1 
	MOVF        R0, 0 
	MOVWF       _h+0 
;Steering Wheel.c,23 :: 		t=value/10%10;
	MOVLW       10
	MOVWF       R4 
	MOVLW       0
	MOVWF       R5 
	MOVF        _value+0, 0 
	MOVWF       R0 
	MOVF        _value+1, 0 
	MOVWF       R1 
	CALL        _Div_16x16_S+0, 0
	MOVLW       10
	MOVWF       R4 
	MOVLW       0
	MOVWF       R5 
	CALL        _Div_16x16_S+0, 0
	MOVF        R8, 0 
	MOVWF       R0 
	MOVF        R9, 0 
	MOVWF       R1 
	MOVF        R0, 0 
	MOVWF       _t+0 
;Steering Wheel.c,24 :: 		u=value%10;
	MOVLW       10
	MOVWF       R4 
	MOVLW       0
	MOVWF       R5 
	MOVF        _value+0, 0 
	MOVWF       R0 
	MOVF        _value+1, 0 
	MOVWF       R1 
	CALL        _Div_16x16_S+0, 0
	MOVF        R8, 0 
	MOVWF       R0 
	MOVF        R9, 0 
	MOVWF       R1 
	MOVF        R0, 0 
	MOVWF       _u+0 
;Steering Wheel.c,26 :: 		RC1_bit=0;
	BCF         RC1_bit+0, 1 
;Steering Wheel.c,27 :: 		RC0_bit=0;
	BCF         RC0_bit+0, 0 
;Steering Wheel.c,28 :: 		PORTE=seg7(th);
	MOVF        _th+0, 0 
	MOVWF       FARG_seg7_num+0 
	MOVLW       0
	MOVWF       FARG_seg7_num+1 
	CALL        _seg7+0, 0
	MOVF        R0, 0 
	MOVWF       PORTE+0 
;Steering Wheel.c,29 :: 		delay_ms(1);
	MOVLW       6
	MOVWF       R12, 0
	MOVLW       48
	MOVWF       R13, 0
L_segl0:
	DECFSZ      R13, 1, 1
	BRA         L_segl0
	DECFSZ      R12, 1, 1
	BRA         L_segl0
	NOP
;Steering Wheel.c,30 :: 		RC1_bit=0;
	BCF         RC1_bit+0, 1 
;Steering Wheel.c,31 :: 		RC0_bit=1;
	BSF         RC0_bit+0, 0 
;Steering Wheel.c,32 :: 		PORTE=seg7(h);
	MOVF        _h+0, 0 
	MOVWF       FARG_seg7_num+0 
	MOVLW       0
	MOVWF       FARG_seg7_num+1 
	CALL        _seg7+0, 0
	MOVF        R0, 0 
	MOVWF       PORTE+0 
;Steering Wheel.c,33 :: 		delay_ms(1);
	MOVLW       6
	MOVWF       R12, 0
	MOVLW       48
	MOVWF       R13, 0
L_segl1:
	DECFSZ      R13, 1, 1
	BRA         L_segl1
	DECFSZ      R12, 1, 1
	BRA         L_segl1
	NOP
;Steering Wheel.c,34 :: 		RC1_bit=1;
	BSF         RC1_bit+0, 1 
;Steering Wheel.c,35 :: 		RC0_bit=0;
	BCF         RC0_bit+0, 0 
;Steering Wheel.c,36 :: 		PORTE=seg7(t);
	MOVF        _t+0, 0 
	MOVWF       FARG_seg7_num+0 
	MOVLW       0
	MOVWF       FARG_seg7_num+1 
	CALL        _seg7+0, 0
	MOVF        R0, 0 
	MOVWF       PORTE+0 
;Steering Wheel.c,37 :: 		delay_ms(1);
	MOVLW       6
	MOVWF       R12, 0
	MOVLW       48
	MOVWF       R13, 0
L_segl2:
	DECFSZ      R13, 1, 1
	BRA         L_segl2
	DECFSZ      R12, 1, 1
	BRA         L_segl2
	NOP
;Steering Wheel.c,38 :: 		RC1_bit=1;
	BSF         RC1_bit+0, 1 
;Steering Wheel.c,39 :: 		RC0_bit=1;
	BSF         RC0_bit+0, 0 
;Steering Wheel.c,40 :: 		PORTE=seg7(u);
	MOVF        _u+0, 0 
	MOVWF       FARG_seg7_num+0 
	MOVLW       0
	MOVWF       FARG_seg7_num+1 
	CALL        _seg7+0, 0
	MOVF        R0, 0 
	MOVWF       PORTE+0 
;Steering Wheel.c,41 :: 		}
	RETURN      0
; end of _segl

_segr:
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

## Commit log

2017-12-29 Initial Commit.
    [3sensor.brd, 3sensor.sch, Assem1.SLDASM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]
2018-01-05 Data Logger Commit
    [DAQ13.brd, DAQ13.sch, DAQBOARD.brd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]
